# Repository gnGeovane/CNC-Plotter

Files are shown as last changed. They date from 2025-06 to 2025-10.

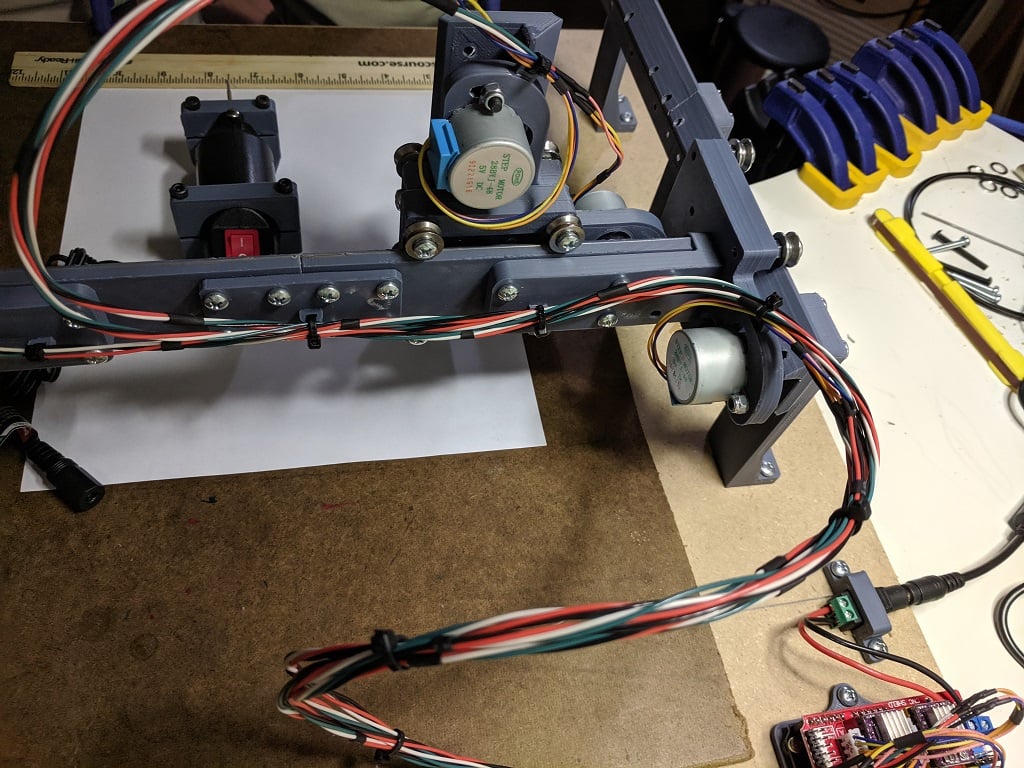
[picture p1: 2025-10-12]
Modelos 3D/Fully 3D Printed Small CNC Router_Plotter - 3842401 - part 1 of 2/images/Back_Overall-1.jpg

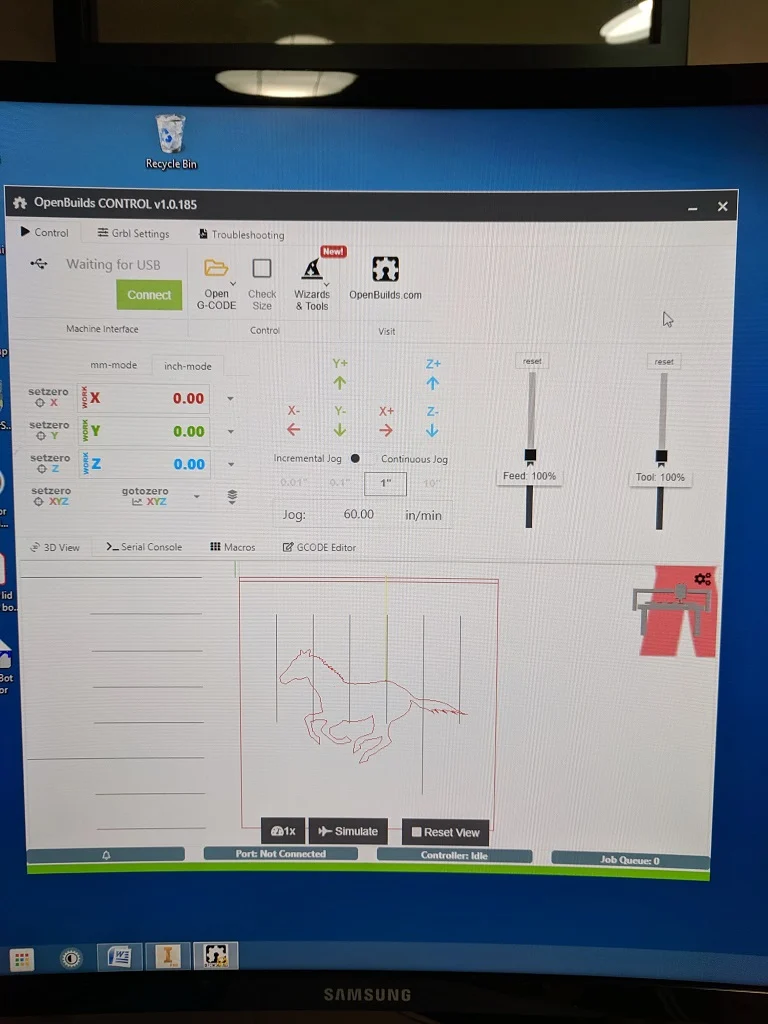
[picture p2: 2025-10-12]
Modelos 3D/Fully 3D Printed Small CNC Router_Plotter - 3842401 - part 1 of 2/images/OpenBuilds_Control_Screen_Shot-1.jpg

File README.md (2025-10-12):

# CNC-Plotter

Aqui você encontrará os arquivos necessários para fazer uma CNC Plotter e controlá-la.

# Código:

Todos os códigos e a biblioteca para motores de passo foram feitos do zero, linha-a-linha, especificamente para este projeto.
  
As versões mais recentes do código para o arduino incluem suporte para:

- Drivers de motores de passo L293D, ULN2803 e ULN2003;
- Sensores de fim de curso;
- Botão stop;
- Controle de motores de passo com ShiftRegister 74595 usando FullSteps e HalfSteps;
- Motores de passo bipolares ou unipolares.

# G-CODE Sender

Captura de tela 2025-06-23 110918

Para a comunicação do computador com o arduino para o envio do G-CODE do desenho, foi feito um G-CODE Sender do zero, programado no processing 4.
Este arquivo, quando executado no compilador processing, cria uma interface gráfica simples mostrando os comandos de controle da CNC, como:

- Movimentar algum eixo;
- Subir e descer a caneta;
- Ir para a posição Home;
- Buscar um arquivo G-CODE no Windows Explorer e iniciar o envio serial.

# APP para android

Também foi criado um app em Kotlin no Android Studio que funciona de forma similar ao programa G-CODE Sender do item anterior. Porém, o diferencial do app para celular é a possibilidade de controlar a máquina à distância via Bluetooth.

Adobe Express - file
<br> Demonstração do app aqui: https://youtu.be/cIXA6mVwmhk

# Criação de G-CODE

Para criar o arquivo de coordenadas (G-CODE) de uma imagem para desenhá-la, é necessário utilizar o software InksCape (gratuito) ou Autodesk ArtCAM (Pago). Caso queira plotar um circuito em uma PCB, poderá converter arquivos Gerber(.gbr) e Excellon(.drl) em G-CODE utilizando o software de código aberto FlatCAM.
  
# Veja os resultados atuais do projeto:

 CNC

IMG_20251009_102834619_HDR

<br> Desenhos

Desenhos

Captura de tela 2025-06-23 113415

# Assista a CNC em ação no YouTube!

[Desenhando ícone do app (controle por Bluetooth com app)](https://youtu.be/TSL-Wnw5sp4)

<a href="https://youtu.be/TSL-Wnw5sp4">
  Desenhando ícone do app
</a>

<br> [Desenhando um avião (controle via porta serial)](https://www.youtube.com/watch?v=H5-JilG_zv4)

<a href="https://www.youtube.com/watch?v=H5-JilG_zv4">
  Desenhando um avião
</a>

<br> [short - Desenhando um touro (Controle via porta serial)](https://www.youtube.com/shorts/jxCdN6tVYik)

<a href="https://www.youtube.com/shorts/jxCdN6tVYik">
  Desenhando um touro
</a>

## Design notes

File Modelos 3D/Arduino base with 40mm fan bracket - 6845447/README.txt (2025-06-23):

Arduino base with 40mm fan bracket by thrly on Thingiverse: https://www.thingiverse.com/thing:6845447

Summary:
An alternative for Andrew Sleigh's brilliant pen plotter (mk.3) arduino/cnc shield box. This is a much quicker print, and leaves the boards open with space for heatsinks and a side bracket for mounting a small 40mm fan. (The fan just runs straight off the 5V/GND pins on the CNC shield).Fan bracket takes M3 bolts/nuts.Details: https://github.com/thrly/plotter

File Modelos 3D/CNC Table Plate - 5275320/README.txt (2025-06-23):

CNC Table Plate by gcarlyle22 on Thingiverse: https://www.thingiverse.com/thing:5275320

Summary:
I made a CNC plotter for PC boards and couldn't find anything to hold them to the bed. So here is my working table.

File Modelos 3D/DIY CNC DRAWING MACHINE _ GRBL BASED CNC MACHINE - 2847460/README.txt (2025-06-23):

DIY CNC DRAWING MACHINE | GRBL BASED CNC MACHINE by electricdiylab on Thingiverse: https://www.thingiverse.com/thing:2847460

Summary:
JLCPCB (10 boards for $ 2) &amp; Free shipping: https://jlcpcb.comhttps://youtu.be/qOcFgiuLx3kMaterial I UsedArduino UNO :- https://www.amazon.in/gp/product/B015C7SC5U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 CNC shield :- https://www.amazon.in/gp/product/B015C7SC5U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 Stepper driver (2qty) :- https://www.amazon.in/gp/product/B015C7SC5U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 pro servo motor :- https://www.amazon.in/gp/product/B015C7SC5U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 SUPPLY  : - https://goo.gl/FKbxF66MM Smooth rod :- https://www.amazon.in/gp/product/B015C7SC5U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 motor :-    https://goo.gl/w9hHG3Timing belt :- https://www.amazon.in/gp/product/B015C7SC5U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 :- https://www.amazon.in/gp/product/B015C7SC5U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 pulley :- https://www.amazon.in/gp/product/B015C7SC5U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 x 20 aluminium frameLink to download : -MI Inkscape Extension.zip : - https://www.mediafire.com/file/9x1m60w1x6tdhaw/MI%20Inkscape%20Extension.zipMIGRBL.zip :-https://www.mediafire.com/file/wxsy99vzdu6dlvg/MIGRBL.zipCNC - Shield v3 01 WIRING.pnghttps://www.mediafire.com/file/53c8ywmb4aw69k9/CNC%20-%20Shield%20v3%2001%20WIRING.pngGRBL Controller :-https://github.com/zapmaker/GrblHoming/releases/download/v3.6.1/GrblController361Setup.exevisit for morehttp://electricdiylab.com/

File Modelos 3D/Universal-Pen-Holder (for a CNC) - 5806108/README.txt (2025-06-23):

Universal-Pen-Holder (for a CNC) by ZenziWerken on Thingiverse: https://www.thingiverse.com/thing:5806108

Summary:
Every now and then I thought about how the CNC machine could be used as a plotter. Of course, the Z-axis, which is driven by a stepper motor, is only conditionally suitable, but at least the positioning accuracy should be clearly superior to the belt-driven plotters. So all that's really missing is a spring-loaded mounting for the pen. This holder is so universal that you can use any pen you like. In a first attempt, I designed a version that accepts a classic Rapidograph (ink pen with capillary nib). But first of all this design was not usable for other pens, furthermore the linear movement was not precise enough.To solve the problem I got a mini linear rail. This was mounted on parts made of PMMA. I have already used this material in other projects. When heated with a heat gun, it can be bent into shape quite well. The result was already good, but the PMMA was not stable enough. Besides, it is difficult to cut threads in PMMA.This is how the final version was made. 3 mm thick aluminum is used. It has slots at the appropriate places, which make cold forming relatively easy. The bending radius is therefore very small. The quite large material thickness allows a reasonable use of taps, so that some screw connections can do without nuts.Please be aware that the stl-file is for viewing purpose only. Don't print this design on a fdm-printer!Visit https://www.zenziwerken.de/en/ for more interesting designs.

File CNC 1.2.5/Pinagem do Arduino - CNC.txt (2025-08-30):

Pinos do Arduino:

----------------------------------------------------------------------------------
11(RX), 12(TX): Módulo Bluetooth (VISÃO DO ARDUINO)
----------------------------------------------------------------------------------
A4, A5:  I2C
----------------------------------------------------------------------------------

----------------------------------------------------------------------------------
0, 1: comunicação serial
----------------------------------------------------------------------------------
2: Sem uso
----------------------------------------------------------------------------------
3: PLANNER
----------------------------------------------------------------------------------
A0:    DUAS FUNÇÕES: PAUSE(click) e AJUSTAR POSIÇÃO(PRESSIONE POR 0,5s)
----------------------------------------------------------------------------------
A1:    SENSOR DE FIM DE CURSO (X0)
----------------------------------------------------------------------------------
A2:    SENSOR DE FIM DE CURSO (Y1)
----------------------------------------------------------------------------------

----------------------------------------------------------------------------------
7, 5, 6, 4: CONTROLE DO EIXO Z
----------------------------------------------------------------------------------
8, 9, 10: SHIFT RETGISTER EIXO X/Y
----------------------------------------------------------------------------------

livres: A3, 13

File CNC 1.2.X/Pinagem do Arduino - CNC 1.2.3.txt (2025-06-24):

Pinos do Arduino:

----------------------------------------------------------------------------------
3(RX), 4(TX): Módulo Bluetooth
----------------------------------------------------------------------------------
A4, A5:  I2C
----------------------------------------------------------------------------------

----------------------------------------------------------------------------------
0, 1: comunicação serial
----------------------------------------------------------------------------------
2: Sem uso
----------------------------------------------------------------------------------
9:    SENSOR DE FIM DE CURSO (X0)
----------------------------------------------------------------------------------
10:    SENSOR DE FIM DE CURSO (Y1)
----------------------------------------------------------------------------------
A0:    AJUSTAR POSIÇÃO (BOT)
----------------------------------------------------------------------------------
A1:    PLANNER
----------------------------------------------------------------------------------

----------------------------------------------------------------------------------
5, 6, 7, 8: IN Z
----------------------------------------------------------------------------------
11, 12, 13:      SHIFT RETGISTER X/Y
----------------------------------------------------------------------------------

livres: A2, A3

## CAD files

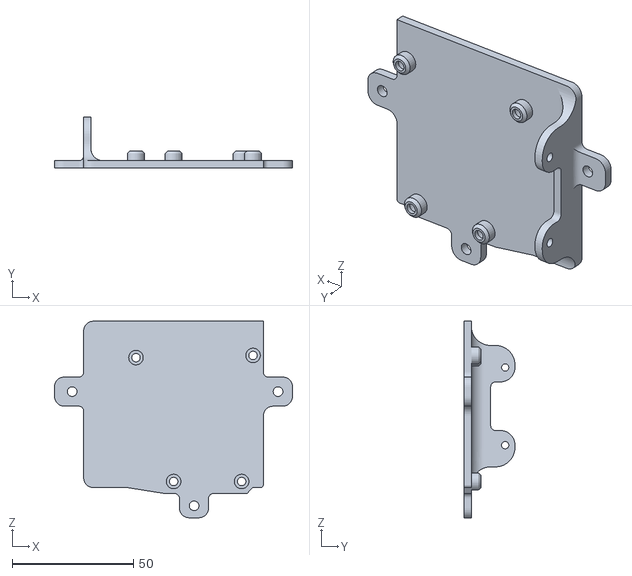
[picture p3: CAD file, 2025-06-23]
Modelos 3D/Arduino base with 40mm fan bracket - 6845447/files/arduino-bracket-with-fan.stl
98.0 x 21.0 x 81.0

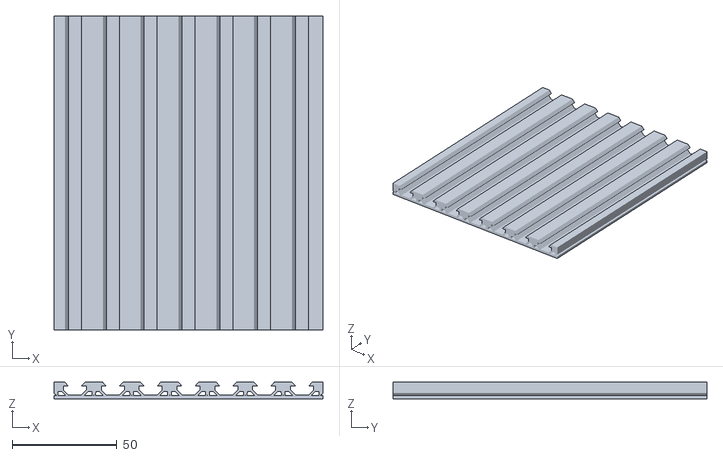
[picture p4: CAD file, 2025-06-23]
Modelos 3D/CNC Table Plate - 5275320/files/Table_V_Slot_Double.stl
128.6 x 150.0 x 7.90

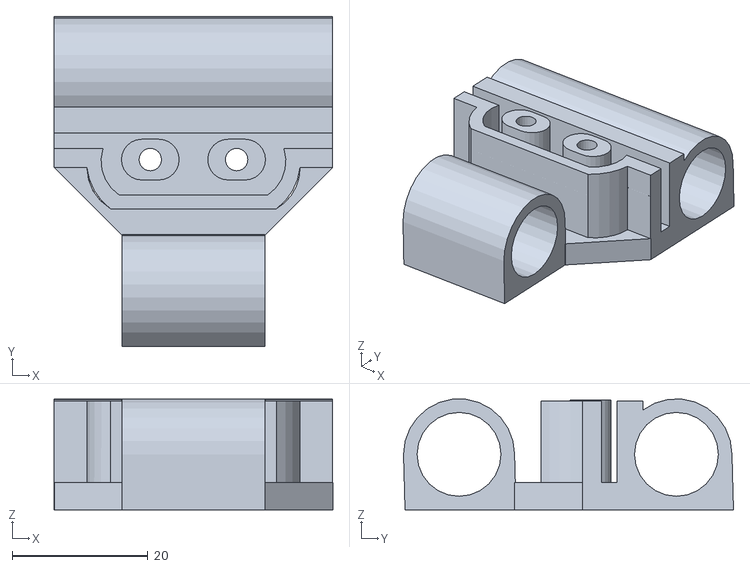
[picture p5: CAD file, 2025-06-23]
Modelos 3D/DIY CNC DRAWING MACHINE _ GRBL BASED CNC MACHINE - 2847460/files/c.stl
41.0 x 48.6 x 16.3

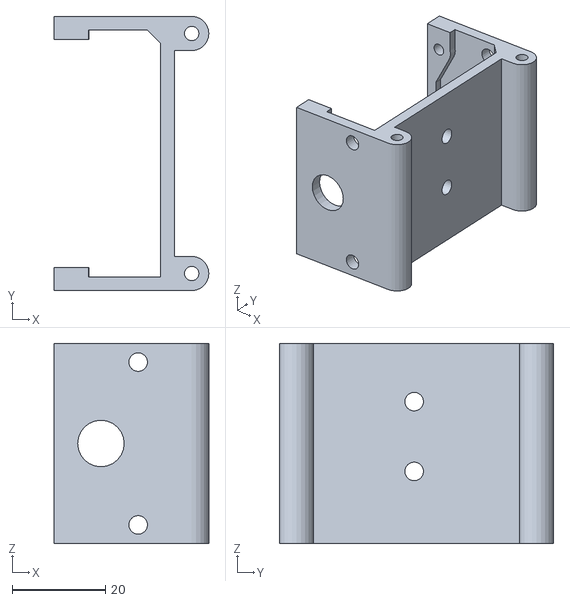
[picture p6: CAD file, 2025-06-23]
Modelos 3D/English and Spanish Mini CNC Plotter With CNC SHIELD, Arduino and Step motor 28BYJ-28 - 2985627/files/X_AXIS_PLATFORMMOD.stl
33.3 x 59.0 x 43.0

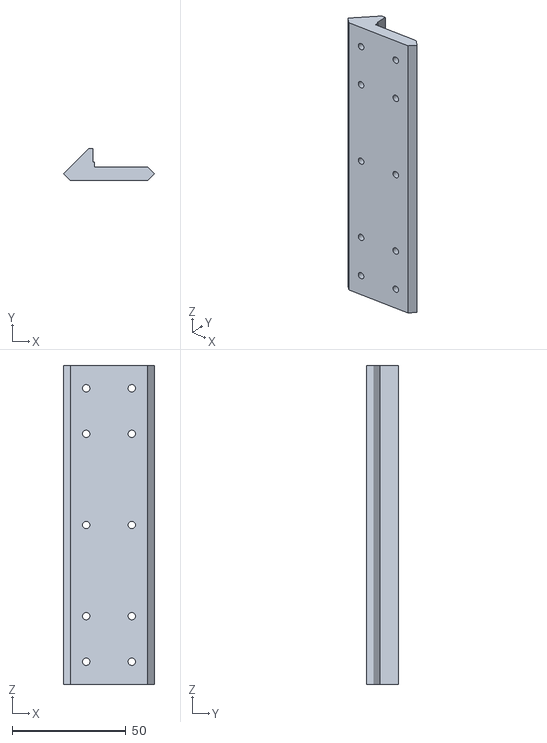
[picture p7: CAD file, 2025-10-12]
Modelos 3D/Fully 3D Printed Small CNC Router_Plotter - 3842401 - part 1 of 2/files/Linear_Rail_140mm.stl
40.0 x 14.0 x 140.0

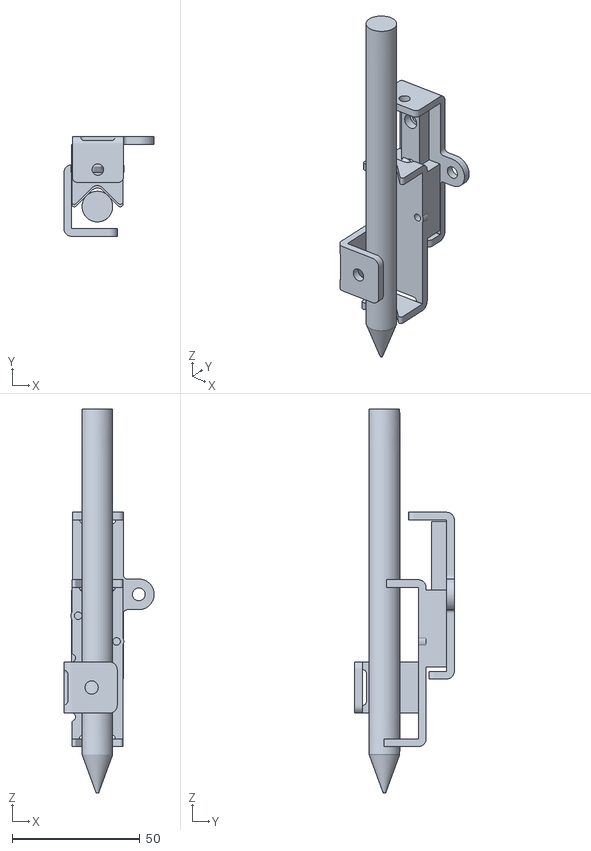
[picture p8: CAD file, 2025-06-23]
Modelos 3D/Universal-Pen-Holder (for a CNC) - 5806108/files/Universal-Pen-Holder.stl
35.3 x 39.0 x 150.0

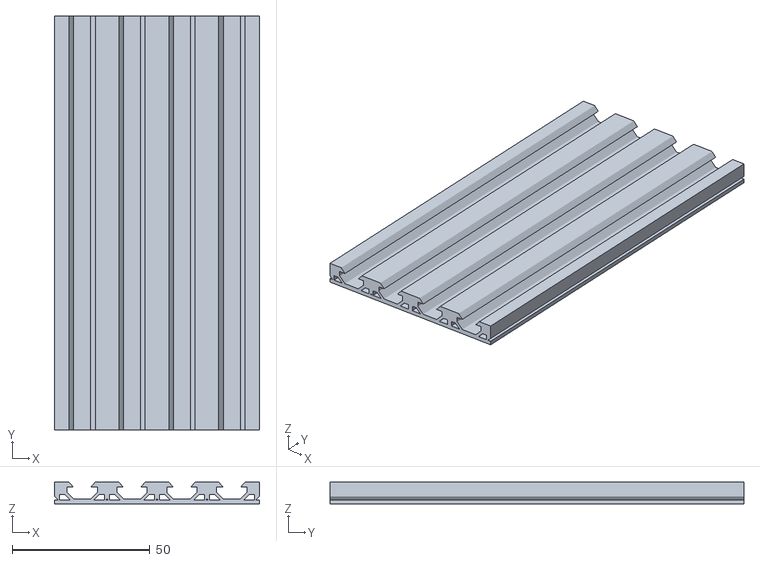
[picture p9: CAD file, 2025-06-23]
Modelos 3D/CNC Table Plate - 5275320/files/Table_V_Slot.stl
74.3 x 150.0 x 7.90

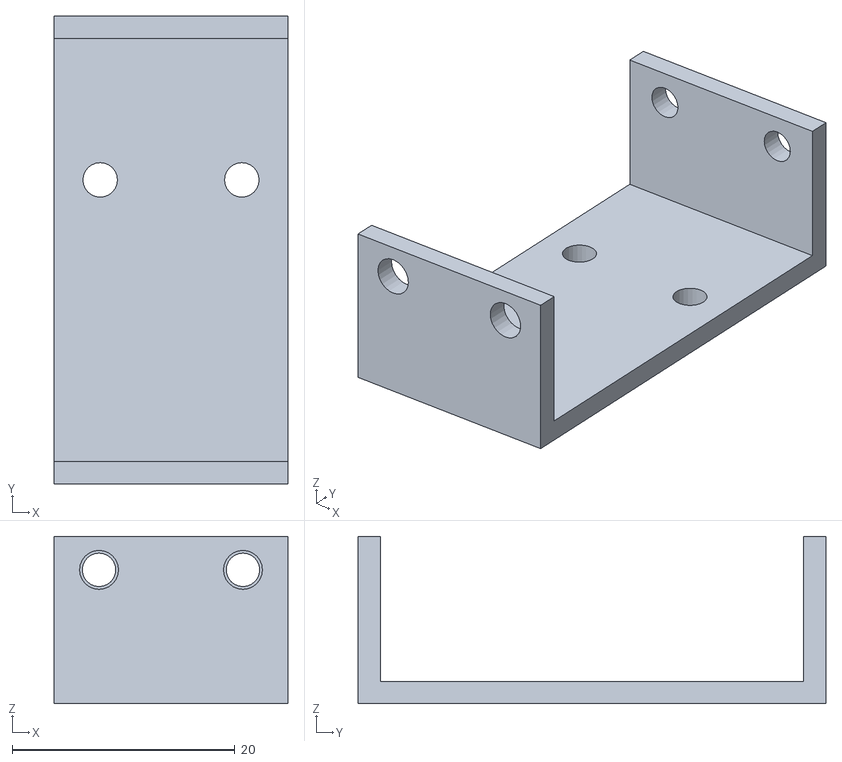
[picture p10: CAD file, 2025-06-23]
Modelos 3D/DIY CNC DRAWING MACHINE _ GRBL BASED CNC MACHINE - 2847460/files/d.stl
21.0 x 42.0 x 15.0

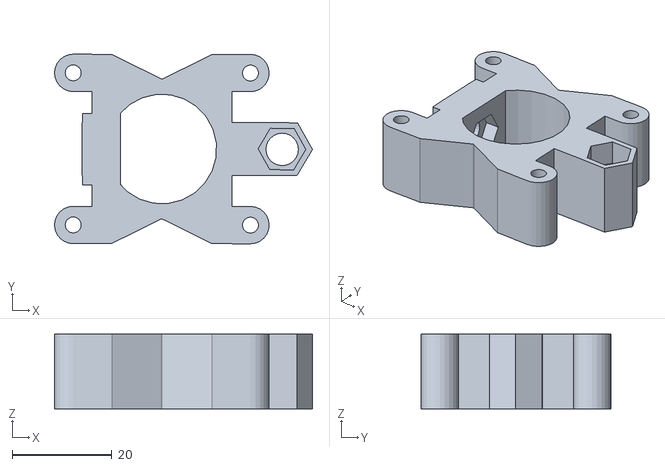
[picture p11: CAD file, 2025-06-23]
Modelos 3D/English and Spanish Mini CNC Plotter With CNC SHIELD, Arduino and Step motor 28BYJ-28 - 2985627/files/Spindle_Holder.stl
51.7 x 38.0 x 15.0

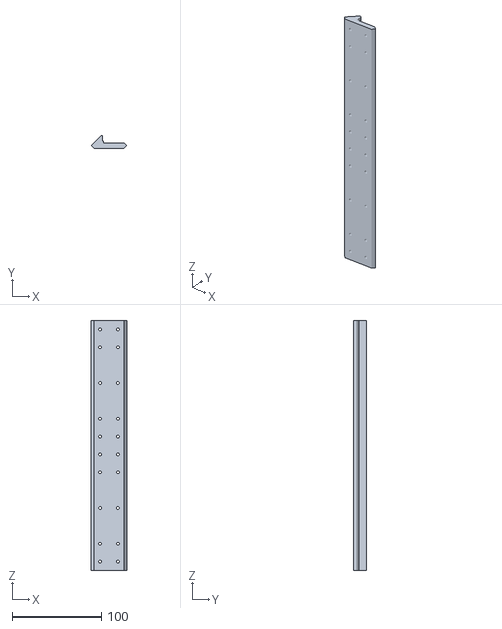
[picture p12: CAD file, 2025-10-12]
Modelos 3D/Fully 3D Printed Small CNC Router_Plotter - 3842401 - part 1 of 2/files/Linear_Rail_280mm.stl
40.0 x 14.0 x 280.0

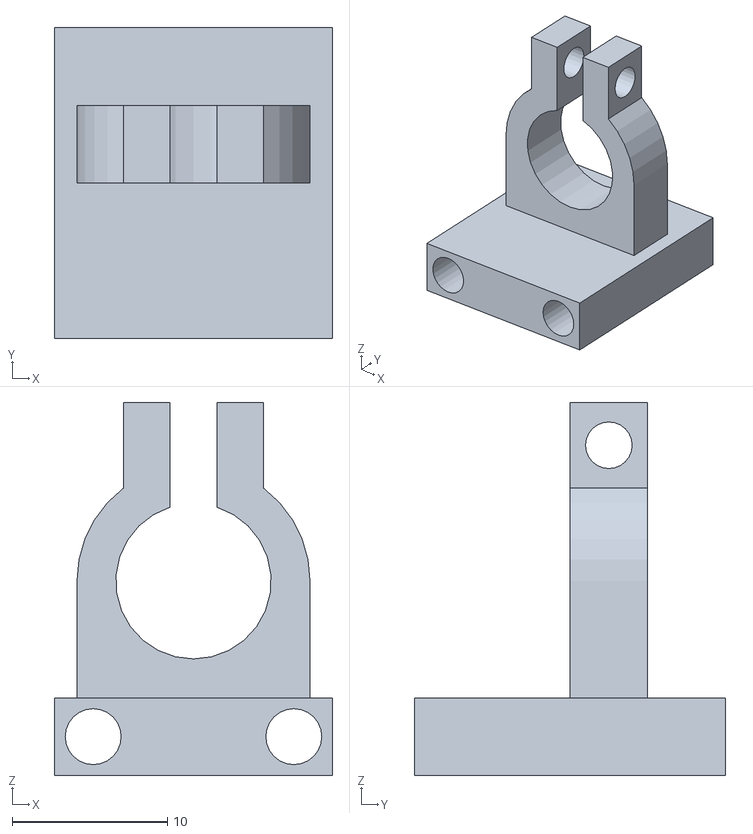
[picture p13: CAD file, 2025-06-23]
Modelos 3D/DIY CNC DRAWING MACHINE _ GRBL BASED CNC MACHINE - 2847460/files/E.stl
17.9 x 20.0 x 24.0

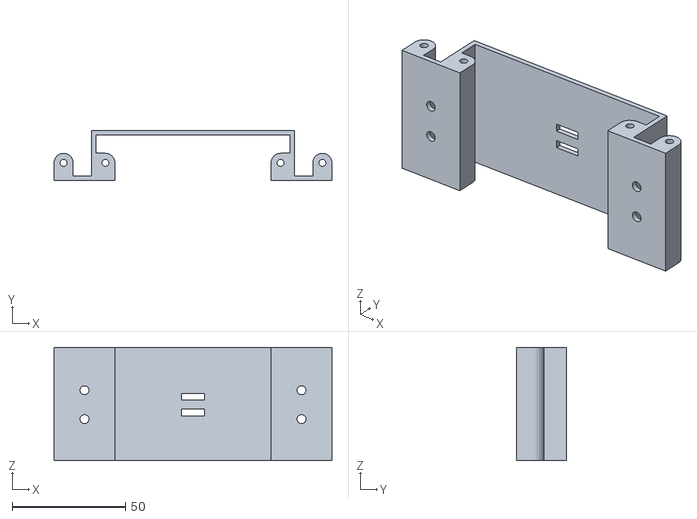
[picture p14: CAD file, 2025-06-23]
Modelos 3D/English and Spanish Mini CNC Plotter With CNC SHIELD, Arduino and Step motor 28BYJ-28 - 2985627/files/Y_Slider_Rail_Unidos.stl
123.0 x 22.0 x 50.0

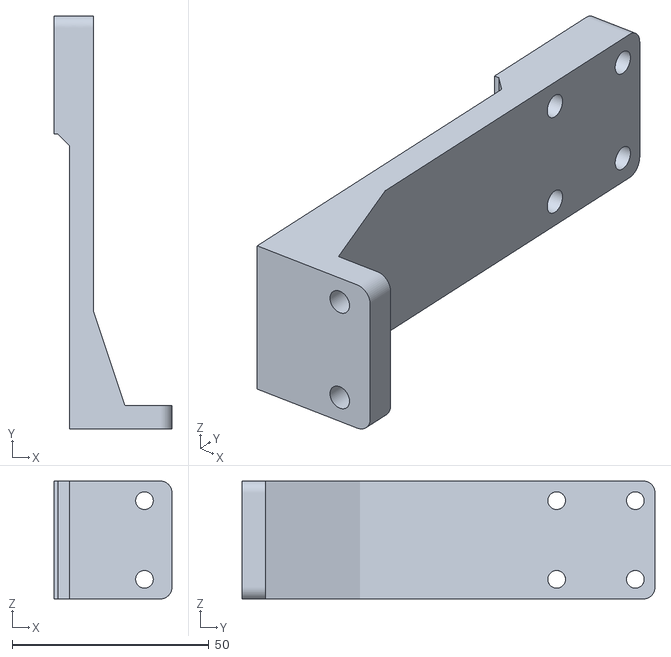
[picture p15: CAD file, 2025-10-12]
Modelos 3D/Fully 3D Printed Small CNC Router_Plotter - 3842401 - part 1 of 2/files/Leg.stl
30.0 x 105.0 x 30.0

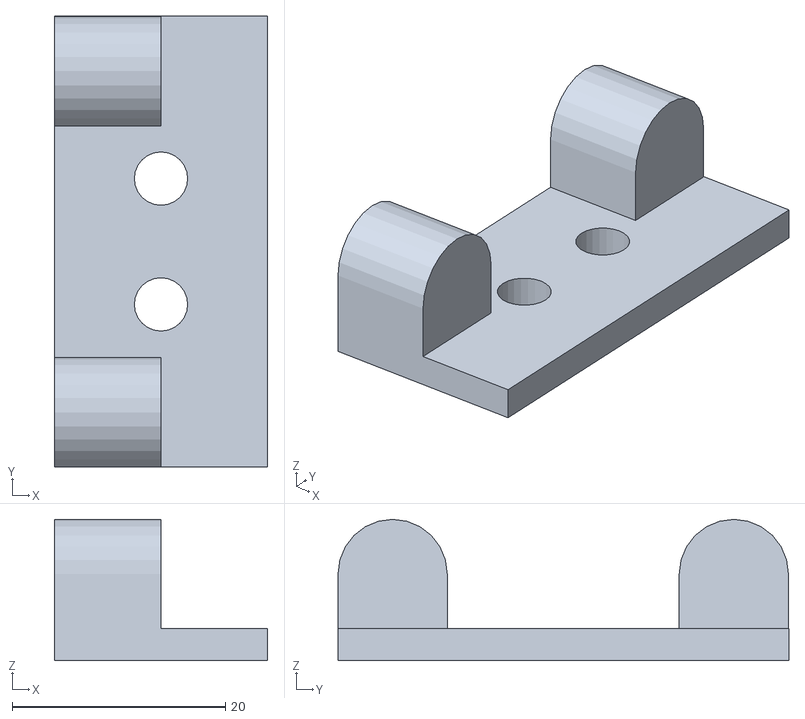
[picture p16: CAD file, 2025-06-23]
Modelos 3D/DIY CNC DRAWING MACHINE _ GRBL BASED CNC MACHINE - 2847460/files/b.stl
20.0 x 42.3 x 13.2

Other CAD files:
Modelos 3D/English and Spanish Mini CNC Plotter With CNC SHIELD, Arduino and Step motor 28BYJ-28 - 2985627/files/Y_Motor_Mount.stl
Modelos 3D/Fully 3D Printed Small CNC Router_Plotter - 3842401 - part 1 of 2/files/Zip_Tie_Holder.stl
Modelos 3D/DIY CNC DRAWING MACHINE _ GRBL BASED CNC MACHINE - 2847460/files/a.stl
Modelos 3D/English and Spanish Mini CNC Plotter With CNC SHIELD, Arduino and Step motor 28BYJ-28 - 2985627/files/YAxis_Rail_Holder_mod.stl
Modelos 3D/English and Spanish Mini CNC Plotter With CNC SHIELD, Arduino and Step motor 28BYJ-28 - 2985627/files/Soporte_para_lapiz.stl
Modelos 3D/English and Spanish Mini CNC Plotter With CNC SHIELD, Arduino and Step motor 28BYJ-28 - 2985627/files/Z_AXIS_MOTOR_COUPLINGmod.stl
Modelos 3D/English and Spanish Mini CNC Plotter With CNC SHIELD, Arduino and Step motor 28BYJ-28 - 2985627/files/x_Motor_Mount.stl
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

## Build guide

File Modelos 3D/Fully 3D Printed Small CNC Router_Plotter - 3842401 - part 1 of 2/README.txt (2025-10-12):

Fully 3D Printed Small CNC Router/Plotter by cbc on Thingiverse: https://www.thingiverse.com/thing:3842401

Summary:
This Thing began as an effort to build a small, cheap CNC machine.  I mainly wanted to gain some experience with the electronics and control software without spending several hundred dollars on components.  For control it uses clones of an Arduino Uno and CNC V3 shield.  Steppers are the ultra cheap 28BYJ-48's with the bipolar hack.  The drive system is GT2 pulleys with belts glued to the linear rails used as a rack and pinion gear drive to reduce moving parts.  For a spindle I would try the tiny HF Drillmaster Rotary Tool (see edit below).  I did not want to buy rods or extrusions for the frame so all the other parts including linear rails would be 3D printed.   Plus all the parts had to fit on the 6"x 6" print bed of the Lulzbot Mini.  This is what I ended up with.  It is fairly small but still has 7"x 7"x 1.5 (177 x 177 x 40 mm) of travel with about 18" x 20" overall size.  It was fairly cheap (by CNC standards anyway).  It cost about $90.00 in purchased parts, plus whatever it cost me to print the parts.   As an exercise in learning the electronics it was excellent.  I learned plenty.  I will try to share what I learned.  It turns out in function it is more of a demo or Toy CNC.  Nod here to Thorgal's ToyREP 3D Printer (see build notes).   It is not really rigid enough to be called a real CNC machine but repeatability is surprisingly good.  It also moves well.  I have done plots at 60 in/min.  It gets glitchy above that but maybe some settings could be tweaked.  To be honest I haven't even tried the rotary tool for milling yet.  I have been focusing on holding pens.  As a pen plotter it is working great!  My granddaughter is fascinated by it and loves watching it draw.  She wants to learn to use it and that makes the whole build a win for me!  If it ever actually mills something or someday holds a laser cutter that will be a bonus.   Video: https://youtu.be/o14qxU9eJ0QRepeatability video: https://youtu.be/fjbzklIJpxMParts:Online Parts:Here are links to the parts I purchased on Amazon.  Cost might be less if you don't mind long ship times.Uno and CNC shield clone Kit:  $18.99This kit comes with limit switches that I have not used yet but will try to incorporate in the future.Stepper Motors  $10.39Steppers come with driver boards that you don't need.  Use the drivers in the CNC kit.  Motors will need to be modified to bipolar. GT2 Timing Belt    $7.99Timing Belt Pulleys   $5.99V Groove Wheels   $8.71Power Supply   $10.99I used a similar one I had on hand)Locally Sourced Parts:Lowes had M4 Phillips head machine screws (12 for $1.98).  You could save money by purchasing those online.  I used the Phillips head because they were cheaper than socket head (socket head screws would look better).  I did use socket head screws where I thought they would be more functional.   Most of those came from Ace Hardware.1/2"x 24"x 24" MDF   $3.84  (cut to required size)Spindle Motor   $9.99  Harbor Freight (less if you find a 25% off coupon)  I am sorry to report the Collet on this tool is not strong enough to hold the end mill in place.  See additional comments below.Build Notes:Motors/Electronics:The motors and electronics were the most difficult part of the build.  Wait, wasn't that why I did the build in the first place?  Anyway....a few lessons learned. I couldn't run the motors directly from the Arduino.  Well I could, but not all together as a CNC machine, you need the CNC Shield and drivers.  The CNC Shield will only drive bipolar steppers and the 28BYJ's are unipolar.  There is a popular hack to convert them to bipolar.  The bipolar hack is pretty straight forward (plenty of info on that online).  The only tricky part is getting the motor wires in the correct order.  I reused the connector.  My wire order is blue-yellow-orange-pink.  You can reverse the connector on the shield to reverse motor direction (lip on top of connector may need to be clipped).  Reversing is required for the cloned Y-axis motor.  I removed the red wire from the connector and cut it on the motor end.  The motor wires need to be cut and extended.  I used some 4 conductor 22 gage wire from the big box.  If you buy cheap clones like I did for the Arduino and CNC shield be careful with pin alignment.  I wasted several hours troubleshooting when one section of shield pins had missed the sockets on the Arduino.   Looked fine from the outside, pins missed to the inside.   The pins had to be straightened on the stepper drivers boards as well.Driving the motors:  Most of the following information I got from Thorgal's ToyREP 3D Printer here on Thingiverse.   I don't think I would ever have gotten my steppers working properly if I had not finally turned up his info on micro-stepping and voltage settings for the 28BYJ-48.  Thank you Thorgal!I did a lot of searches for 28BYJ-48 &amp; CNC.  Some of the info out there was good, some not so good.  Most of the mistakes were probably mine.  Bipolar Hack - good info.  How to adjust current on stepper driver - good info (but what is the correct setting for a 28BYJ?).  Don't need to micro-step a 28BYJ.  Bad info.  Theory says the 5.625 degree step angle divided by the 1:64 gear reduction give a full step as .088 degrees or 4096 steps per rev.  Those are pretty small full steps.  Probably works for straight Arduino control.  My motors didn't care.  Motors chattered, missed steps, ran slow and hot.  Set micro-stepping to 16 (jumper on shield).  Set voltage on driver board pots to .08 volts.  Motors run smooth, fast and cool.  Thanks again Thorgal!Control Software:I am using GRBL v1.1h (grbl_v1.1h.20190825.hex) loaded with Xloader to the Arduino.   There are plenty of tutorials on using Xloader.  The link to the original Xloader seems to be broken so I will upload a copy of the zip file.   Make sure the baud rate is set to 115200 in the Arduino serial monitor.  If it is set to 9600 you see 2 backward question marks when it tries to connect.  You should see "Grbl 1.1h ['$' for help]".  I am using the OpenBuilds Controller software on the computer to send G code and control the CNC.  This seems to be very nice software with lots of features and it looks good.  This only supports the 115200 baud rate and won't work with earlier versions of Grbl at 9600.  Grbl settings: Check the Axis directions and invert (or reverse the motor plugs) as required, steps/mm X, Y &amp; Z = 1024, acceleration X &amp;Y = 30, Z = 20.  Write down or copy your settings.  If you need to reload (or on some resets) Grbl you will lose your settings.For CAM I use Inventor (or Fusion 360) HSM with the Grbl milling post processor.  Set Output M6 and Output Tool Number to NO in the post processor dialog box in HSM.3D printed Parts:In addition to uploading the STL files I will be uploading STP and native Inventor files to facilitate modifications.  I will also include a 280 liner rail that can be printed in one piece on a larger (12"x 12") print bed.  I will also upload PDF files with a complete bill of materials and drawings with assembly instructions.Orientation on the build plate is straight forward.  I have posted a PDF with build orientation.  No supports were used for any of the parts.   I did set perimeter walls to 4.  This puts a little more material around the holes for tapping threads.  I have a .5mm nozzle.  I used 4 top and bottom layers with .25mm layer height.  I used ABS for all the parts.  Stiffer material like PLA or Nylon X might be better, but I tend to print everything in ABS.I was planning on switching out the pen holder and the spindle holder on the Z rail but now I am thinking it will be easier and quicker to print a Z rail for each holder and swap the rail and all.I am going to post the pen holder and the spindle holder as separate Things to try and keep this one organized.Link to Pen Holder here.Link to Spindle Holder here.Link to Dremel 2050 Stylo Spindle Holder here.Misc:To glue the GT-2 Belt to the Linear Rails I used Dap Rapidfuse.  I found it at the big boxes and it seems to do an excellent job gluing different materials together.  Use the small step on linear rail to help line the belt up.  Roll some of the belt back, apply glue to the rail and roll the belt back down.   When gluing the belt to the Y-axis rails try to start the first tooth in the same place.  This will help keep the X-axis square.  Remember the Y-axis rails are opposite hand.Use the Zip Tie Mounts and Zip Tie Holder(s) for cable management.  They are not shown on the drawings.  To glue Zip Tie Mounts to the drive carriages or X-axis rail use Plastruct Bondene.   The Zip Tie Holder is designed for a #4 flat head screw but I just glued it to the MDF with Rapidfuse.I am using a piece of 1/8" masonite clamped on top of the MDF as a replaceable spoil board.  The masonite is smoother than the MDF and pens write better on it.  They would probably write even better on acrylic.This is a work in progress and I will try post and new info and improvements as I go.  Any comments and suggestions for improvements would be welcome.Edit 9-3-19:  Added link to pen holdersAdded Link to Spindle Holder.Added Repeatability videoEdit 9-6-19:  The spindle Motor from Harbor Freight has a problem. The power is ok.  The problem is the collet on this tool is not strong enough to hold the end mill in place.  I was test milling on 1/8" acrylic.  I was able to mill the acrylic with shallow depth of cuts and was pleasantly surprised at how well it was cutting.  The problem was with holding the end mill in the collet.  I was using a .073" dia. (.125" shank) single flute end mill.  As I was running additional tests suddenly the mill would bury itself in the material.  The end mill was pulling itself out of the collet.  I tried to tighten the the knurled collet with pliers but it still pulled out.  Then I managed to damage the locking pin that keeps the shaft from turning so it no longer locks.  Time for a redesign using a tool with a better collet.  My searches turned up cheap tools but many comments on cheap collets.  Now I am looking at the Dremel Stylo 2050-15. It's 50 bucks.  That's more than half of what I had in the whole build.  Would be nice to be able to cut acrylic though.  If you only cut soft material like machinable wax the HF tool might work. Edit 9-12-2019:  Changed License type to Creative Commons - AttributionEdit 9-27-2019:  Added link to Dremel 2050 Stylo Spindle Holder

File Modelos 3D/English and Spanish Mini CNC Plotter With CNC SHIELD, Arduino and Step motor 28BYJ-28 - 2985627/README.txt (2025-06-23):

English and Spanish Mini CNC Plotter With CNC SHIELD, Arduino and Step motor 28BYJ-28 by lolivet on Thingiverse: https://www.thingiverse.com/thing:2985627

Summary:
EnglishMINI CNC Hi-TechWelcome to the Hi-Tech Electronics and Robotics tutorial to assemble our own small CNC machine for plotting ormill PCB boardsFirst we must have all the printed pieces which must have the following order:1 pcs X AXIS PLATAFORMMOD1 pcs Splindle Holder1 pcs Y Slider Rail Unidos4 pcs Yaxis Rail Holder Mod1 pcs Y Motor Mount1 pcs X Motor Mount1 pcs Soporte para Lapiz1 pcs Z AXIS MOTOR CouplingmodNOTE: All parts must be printed at 50% infill with a resolution of0.25mm (Layer Hight), 2 perimeters, 3 Top Solid Layers and 3 Bottom Solid Layer.If you want us to print it, it would be for a price of: Q410.00List of electronic and mechanical components of the CNC1 pcs CNC Shield with Arduino Uno R3 and 3 Original A4988 Drivers (Q350.00)3 pcs Stepper motors 28byj-48 hacked (Q45.00 C / U)1 pcs 9V Power Supply (Printer Source Q85.00)1 pcs 2 meters of toothed belt GT2 with 2 toothed pulleys (Q100.00)2 pcs 608z circular bearings without printing (Q30.00 C / U)28 Screws with nut M3 (Q2.50 C / U)10 Screws with nut M5 (Q2.75 C / U)NOTE: for the circular bearings, look for the pulley on the thing that you like the most.Help me grow my patreonhttps://www.patreon.com/lolivet/Assembly instructions watch the video.https://youtu.be/sw-cIN33urcEspañol MINI CNC Hi-TechBienvenido al tutorial de Electrónica y Robótica Hi-Techpara armar nuestra propia maquina CNC pequeña para plotear ohacer scarve en nuestras placas PCBPrimero debemos tener todas las piezas impresas las cuales deben tenerel siguiente Orden:1   X AXIS PLATAFORMMOD1   Splindle Holder1   Y Slider Rail Unidos4   Yaxis Rail Holder Mod1   Y Motor Mount1   X Motor Mount1   Soporte para Lapiz1   Z AXIS MOTOR CouplingmodNOTA: Todas las piezas se deben imprimir a 50% de infill con una resolucion de0.25mm (Layer Hight), 2 perimetros, 3 Top Solid Layers y 3 Bottom Solid Layer.Si quires que nosotros te lo imprimamos, seria por un precio de: Q410.00Listado de componentes electronicos y mecanicos de la CNC1   CNC Shield con Arduino Uno R3 y 3 Drivers A4988 Originales (Q350.00)3   Motor Stepp 28byj-48 hackeado (Q45.00 C/U)1   Fuente de Alimentacion 9V (Fuente de Impresora Q85.00)1   2 metros de correa dentada GT2 con 2 poleas dentadas (Q100.00)2   Rodamientos circulares 608z sin impresión (Q30.00 C/U)28  Tornillos con tuerca M3 (Q2.50 C/U)10  Tornillos con tuerca M5 (Q2.75 C/U)NOTA: para los rodamientos circulares buscar en thingivierse la polea que mas te guste.Ayudame a crecer se mi patreonhttps://www.patreon.com/lolivet/Instrucciones para ensamble ver el vídeo.https://youtu.be/sw-cIN33urc

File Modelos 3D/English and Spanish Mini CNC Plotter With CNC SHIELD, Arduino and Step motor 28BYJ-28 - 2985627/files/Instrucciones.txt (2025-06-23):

MINI CNC Hi-Tech
Bienvenido al tutorial de Electrónica y Robótica Hi-Tech
para armar nuestra propia maquina CNC pequeña para plotear o 
hacer scarve en nuestras placas PCB

Primero debemos tener todas las piezas impresas las cuales deben tener 
el siguiente Orden:

1	X AXIS PLATAFORMMOD
1	Splindle Holder
1	Y Slider Rail Unidos
4	Yaxis Rail Holder Mod
1	Y Motor Mount
1	X Motor Mount
1	Soporte para Lapiz
1	Z AXIS MOTOR Couplingmod

NOTA: Todas las piezas se deben imprimir a 50% de infill con una resolucion de 
0.25mm (Layer Hight), 2 perimetros, 3 Top Solid Layers y 3 Bottom Solid Layer.
Si quires que nosotros te lo imprimamos, seria por un precio de: Q410.00

Listado de componentes electronicos y mecanicos de la CNC

1	CNC Shield con Arduino Uno R3 y 3 Drivers A4988 (Q350.00)
3	Motor Stepp 28byj-48 hackeado (Q45.00 C/U)
1	Fuente de Alimentacion 9V (Fuente de Impresora Q85.00)
1	2 metros de correa dentada GT2 con 2 poleas dentadas (Q100.00)
2	Rodamientos circulares 608z sin impresion (Q30.00 C/U)
28	Tornillos con tuerca M3 (Q2.50 C/U)
10	Tornillos con tuerca M5 (Q2.75 C/U)

NOTA: para los rodamientos circulares buscar en thingivierse la polea que mas te guste.

Instrucciones para ensamble Ver el video.

Acá te dejo la descargas para que puedas utilizar tu mini cnc una vez armada

Librería GRBL que deberás cargar en el Arduino para que reconozca la CNC Shield y los motores:

http://www.mediafire.com/file/u5dwi73bba91fo0/GRBL%20para%20Arduino.rar

Programa para poder configurar y operar nuestra MINI CNC

http://www.mediafire.com/file/i7xlj4s27cp373v/GrblController361Setup.rar
http://www.mediafire.com/file/2b5i38sofgz7rwu/UniversalGcodeSender.zip
http://www.mediafire.com/file/ac3m6jhl83z3uah/ugsplatform.zip (este es el que mas recomiendo).

y por ultimo el programa utilizado para generar los archivos a dibujar
http://www.mediafire.com/file/1gl1vqsds2q9c3y/inkscape-0.92.3-x64.rar

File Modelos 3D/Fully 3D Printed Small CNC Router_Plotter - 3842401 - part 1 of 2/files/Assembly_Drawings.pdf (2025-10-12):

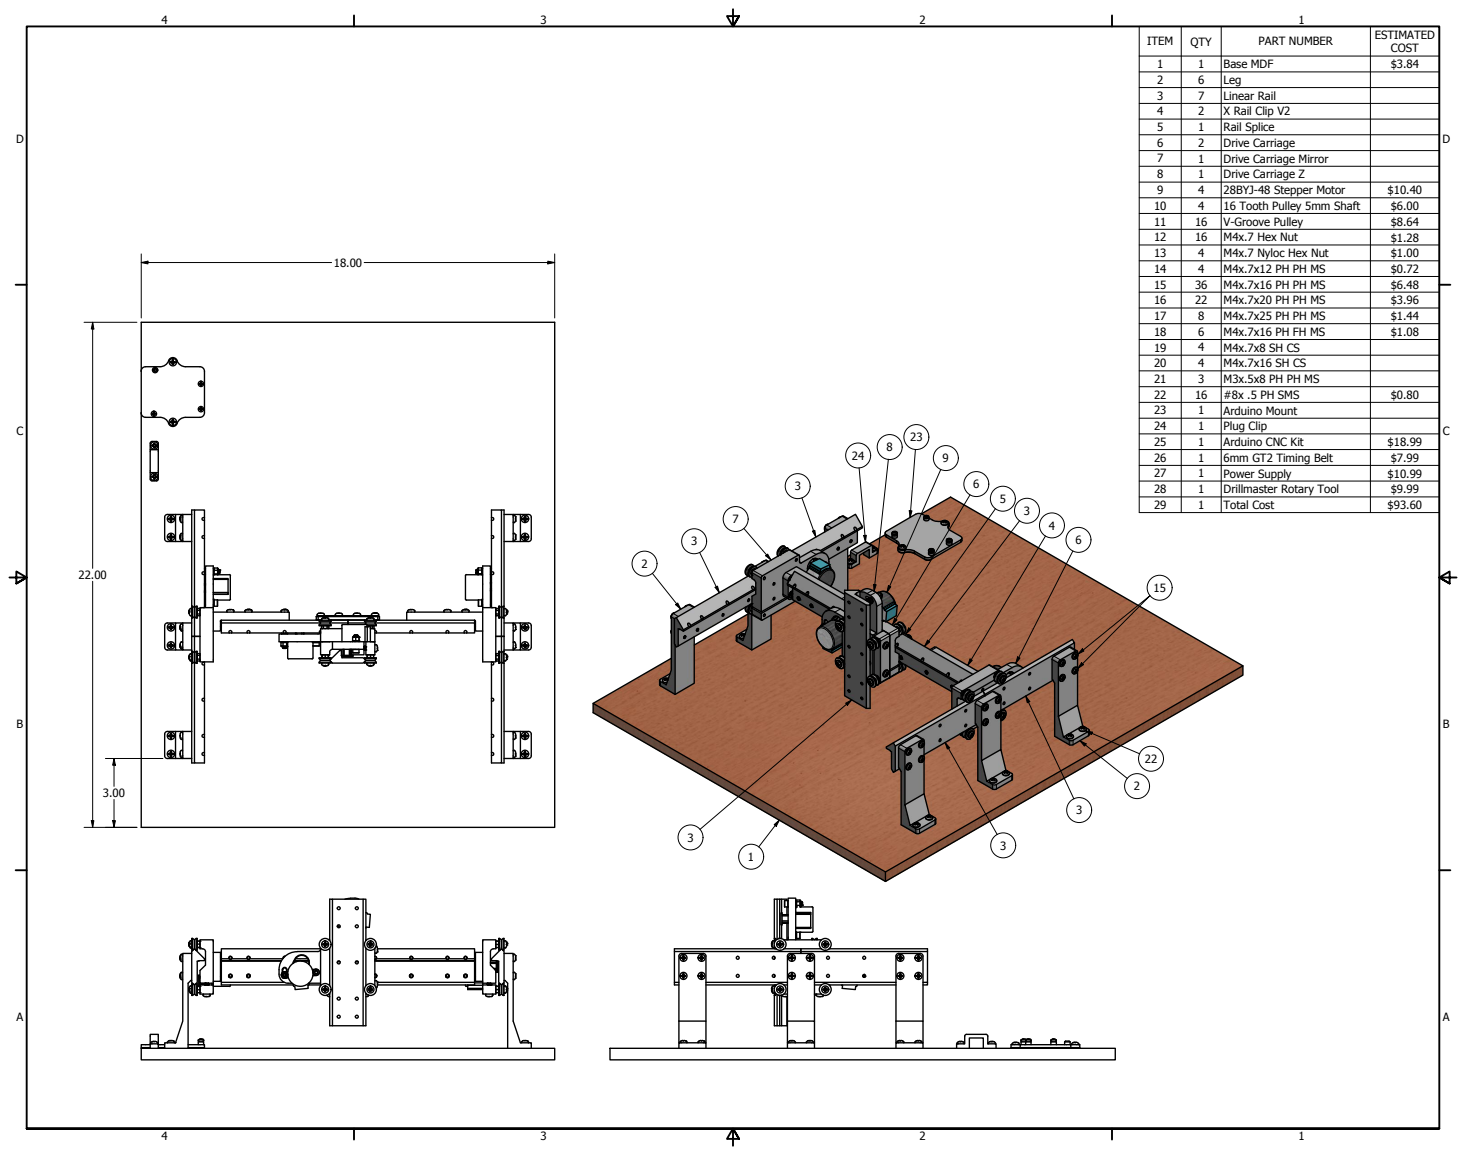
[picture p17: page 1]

B a s e M D F | $ .
L e g

3 | 7 2 | L X Rail Clip i n e a r R a il 4

5 | 1 | R a il S pli c e
6 | 2 | D r i v e C a r r i a g e
7 | 1 | D r i v e C a r r i a g e M i r r o r
8 | 1 | D r i v e C a r r i a g e Z
9 | 4 | 2 8 B YJ -4 8 S t e p p e r M o t o r | $ 1 0 . 4 0
1 0 | 4 | 1 6 T o o t h P ulle y 5 m m S h a ft | $ 6 . 0 0
1 1 | 1 6 | V -G r o o v e P ulle y | $ 8 . 6 4
1 2 | 1 6 | M 4 x . 7 H e x N u t | $ 1 . 2 8
1 3 | 4 | M 4 x . 7 N ylo c H e x N u t | $ 1 . 0 0
1 4 | 4 | M 4 x . 7 x 1 2 P H P H M S | $ 0 . 7 2
1 5 | 3 6 | M 4 x . 7 x 1 6 P H P H M S | $ 6 . 4 8
1 6 | 2 2 | M 4 x . 7 x 2 0 P H P H M S | $ 3 . 9 6
1 7 | 8 | M 4 x . 7 x 2 5 P H P H M S | $ 1 . 4 4
1 8 | 6 | M 4 x . 7 x 1 6 P H F H M S | $ 1 . 0 8
1 9 | 4 | M 4 x . 7 x 8 S H C S
2 0 | 4 | M 4 x . 7 x 1 6 S H C S
2 1 | 3 | M 3 x . 5 x 8 P H P H M S
2 2 | 1 6 | # 8 x . 5 P H S M S | $ 0 . 8 0
2 3 | 1 | A r d u i n o M o u n t
2 4 | 1 | Plu g Cli p
2 5 | 1 | A r d u i n o C N C K i t | $ 1 8 . 9 9
2 6 | 1 | 6 m m G T 2 T i m i n g B elt | $ 7 . 9 9
2 7 | 1 | P o w e r S u p ply | $ 1 0 . 9 9
2 8 | 1 | D r illm a s t e r R o t a r y T o ol | $ 9 . 9 9
2 9 | 1 | T o t al C o s t | $ 9 3 . 6 0

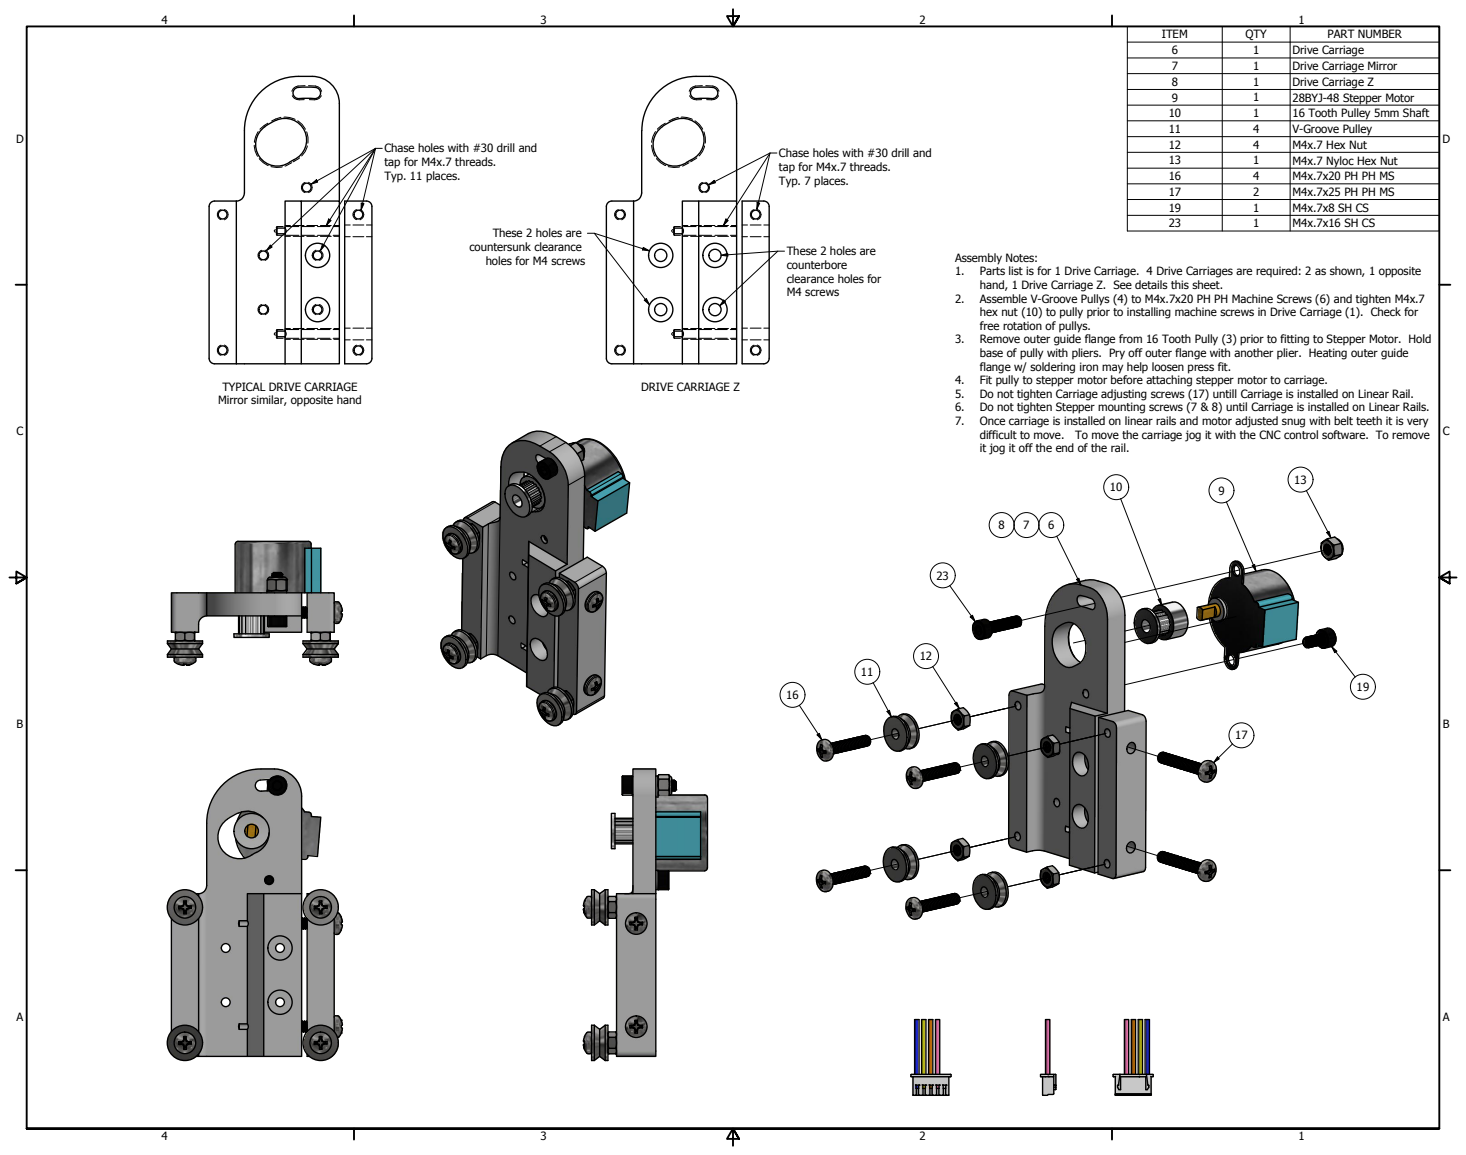
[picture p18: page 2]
DRIVE CARRIAGE Z

ITEM | QTY | PART NUMBER
6 | 1 | Drive Carriage
7 | 1 | Drive Carriage Mirror
8 | 1 | Drive Carriage Z
9 | 1 | 28BYJ-48 Stepper Motor
10 | 1 | 16 Tooth Pulley 5mm Shaft
11 | 4 | V-Groove Pulley
12 | 4 | M4x.7 Hex Nut
13 | 1 | M4x.7 Nyloc Hex Nut
16 | 4 | M4x.7x20 PH PH MS
17 | 2 | M4x.7x25 PH PH MS
19 | 1 | M4x.7x8 SH CS
23 | 1 | M4x.7x16 SH CS

Chase holes with #30 drill and
tap for M4x.7 threads.
Typ. 11 places.

Typ. 7 places.

These 2 holes are
countersunk clearance
holes for M4 screws

counterbore
clearance holes for
M4 screws

Assembly Notes:
1. Parts list is for 1 Drive Carriage. 4 Drive Carriages are required: 2 as shown, 1 opposite
hand, 1 Drive Carriage Z. See details this sheet.
2. Assemble V-Groove Pullys (4) to M4x.7x20 PH PH Machine Screws (6) and tighten M4x.7
hex nut (10) to pully prior to installing machine screws in Drive Carriage (1). Check for
free rotation of pullys.
3. Remove outer guide flange from 16 Tooth Pully (3) prior to fitting to Stepper Motor. Hold
base of pully with pliers. Pry off outer flange with another plier. Heating outer guide
flange w/ soldering iron may help loosen press fit.
4. Fit pully to stepper motor before attaching stepper motor to carriage.
5. Do not tighten Carriage adjusting screws (17) untill Carriage is installed on Linear Rail.
6. Do not tighten Stepper mounting screws (7 & 8) until Carriage is installed on Linear Rails.
7. Once carriage is installed on linear rails and motor adjusted snug with belt teeth it is very
difficult to move. To move the carriage jog it with the CNC control software. To remove
it jog it off the end of the rail.

TYPICAL DRIVE CARRIAGE
Mirror similar, opposite hand

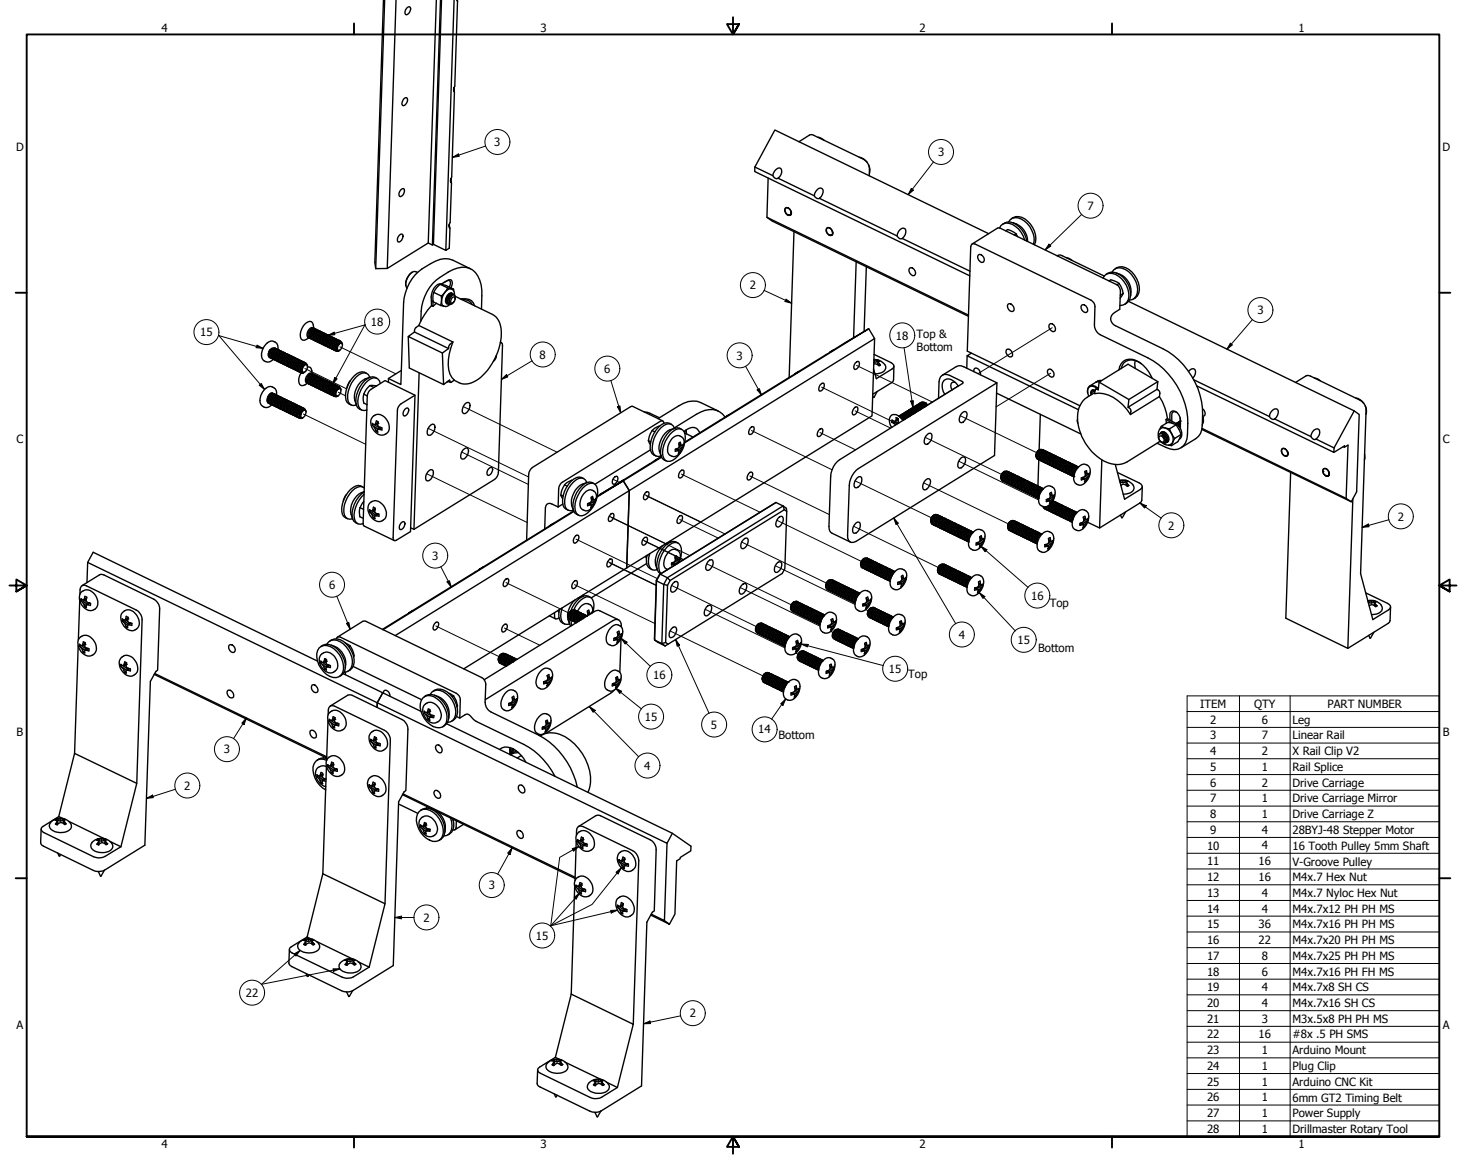
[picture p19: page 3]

I T E M | Q TY | P A RT N U M B E R
2 | 6 | L e g
3 | 7 2 | L X Rail Clip i n e a r R a il 4

5 | 1 | R a il S pli c e
6 | 2 | D r i v e C a r r i a g e
7 | 1 | D r i v e C a r r i a g e M i r r o r
8 | 1 | D r i v e C a r r i a g e Z
9 | 4 | 2 8 B YJ -4 8 S t e p p e r M o t o r
1 0 | 4 | 1 6 T o o t h P ulle y 5 m m S h a ft
1 1 | 1 6 | V -G r o o v e P ulle y
1 2 | 1 6 | M 4 x . 7 H e x N u t
1 3 | 4 | M 4 x . 7 N ylo c H e x N u t
1 4 | 4 | M 4 x . 7 x 1 2 P H P H M S
1 5 | 3 6 | M 4 x . 7 x 1 6 P H P H M S
1 6 | 2 2 | M 4 x . 7 x 2 0 P H P H M S
1 7 | 8 | M 4 x . 7 x 2 5 P H P H M S
1 8 | 6 | M 4 x . 7 x 1 6 P H F H M S
1 9 | 4 | M 4 x . 7 x 8 S H C S
2 0 | 4 | M 4 x . 7 x 1 6 S H C S
2 1 | 3 | M 3 x . 5 x 8 P H P H M S
2 2 | 1 6 | # 8 x . 5 P H S M S
2 3 | 1 | A r d u i n o M o u n t
2 4 | 1 | Plu g Cli p

A r d u i n o C N C K i t
m m G T T i m i n g B elt
P o w e r S u p ply
D r illm a s t e r R o t a r y T o

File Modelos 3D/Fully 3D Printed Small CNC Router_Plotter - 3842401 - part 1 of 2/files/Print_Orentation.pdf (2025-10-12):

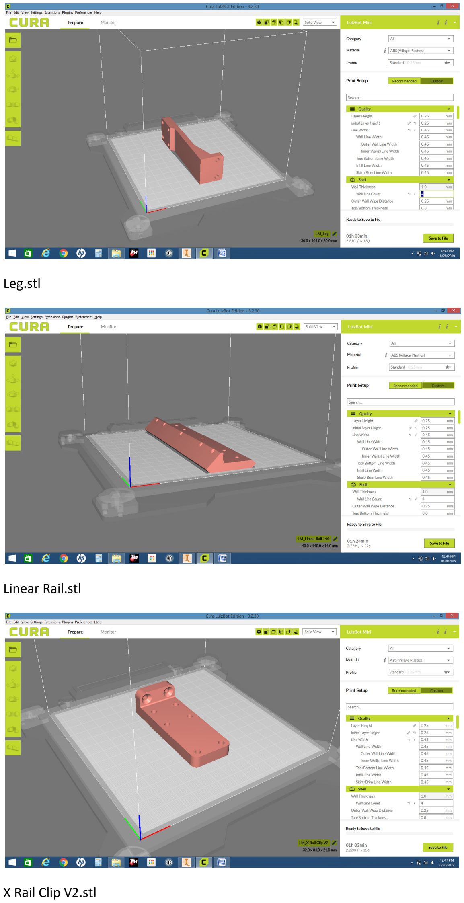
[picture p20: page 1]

Leg.stl

Linear Rail.stl

X Rail Clip V2.stl

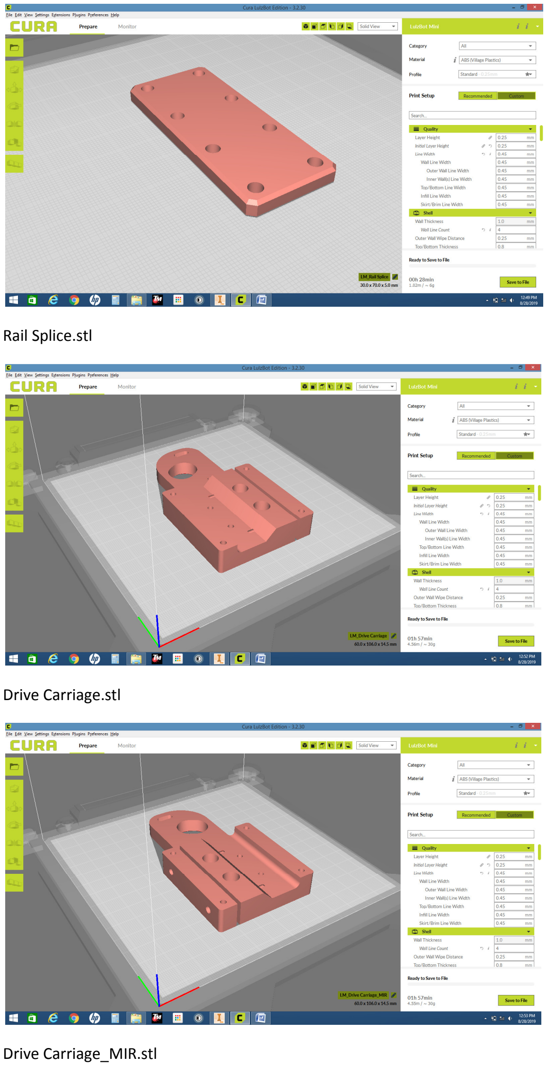
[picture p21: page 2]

Rail Splice.stl

Drive Carriage.stl

Drive Carriage_MIR.stl

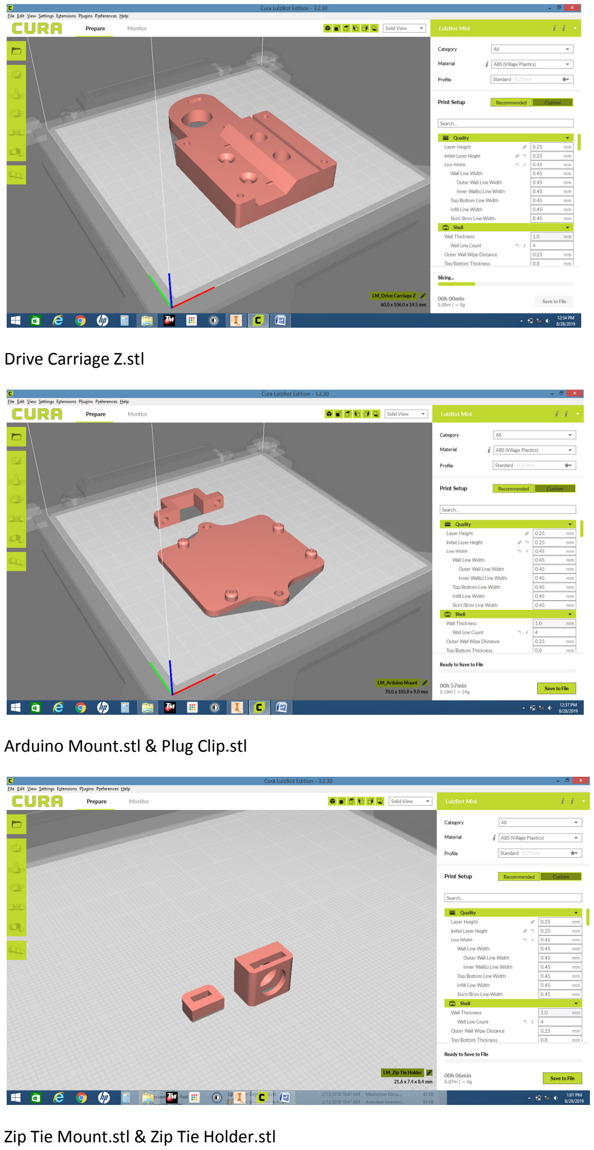
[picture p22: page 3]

Drive Carriage Z.stl

Arduino Mount.stl & Plug Clip.stl

Zip Tie Mount.stl & Zip Tie Holder.stl

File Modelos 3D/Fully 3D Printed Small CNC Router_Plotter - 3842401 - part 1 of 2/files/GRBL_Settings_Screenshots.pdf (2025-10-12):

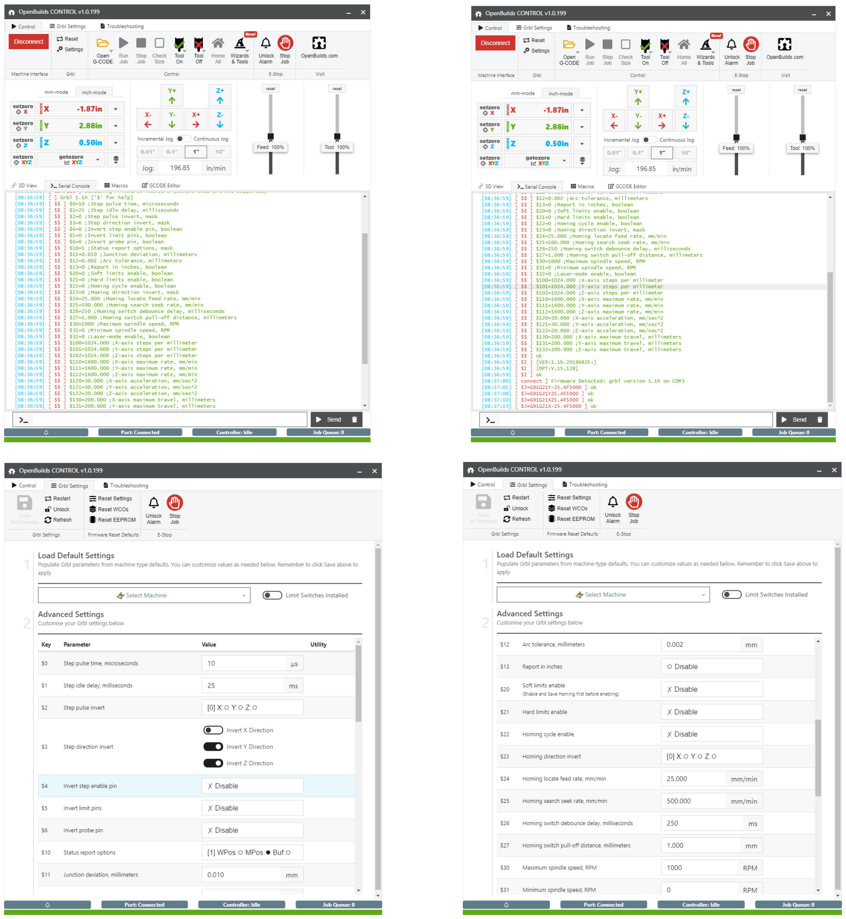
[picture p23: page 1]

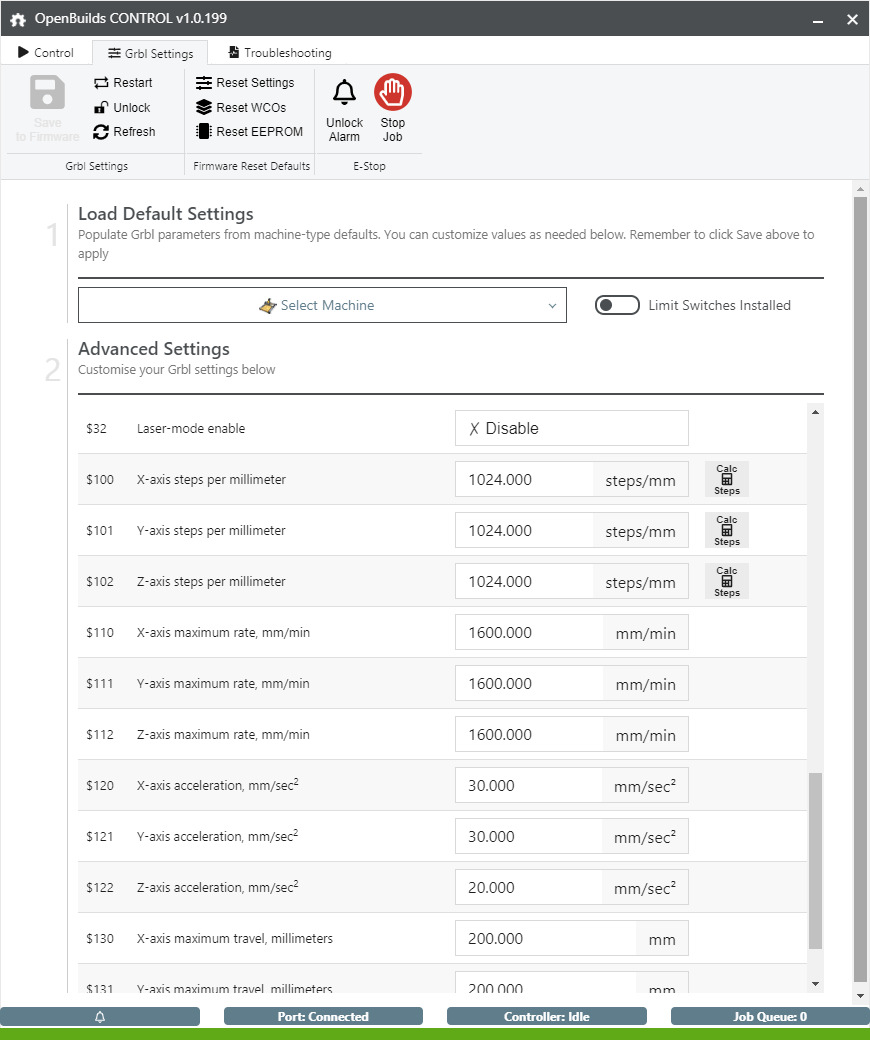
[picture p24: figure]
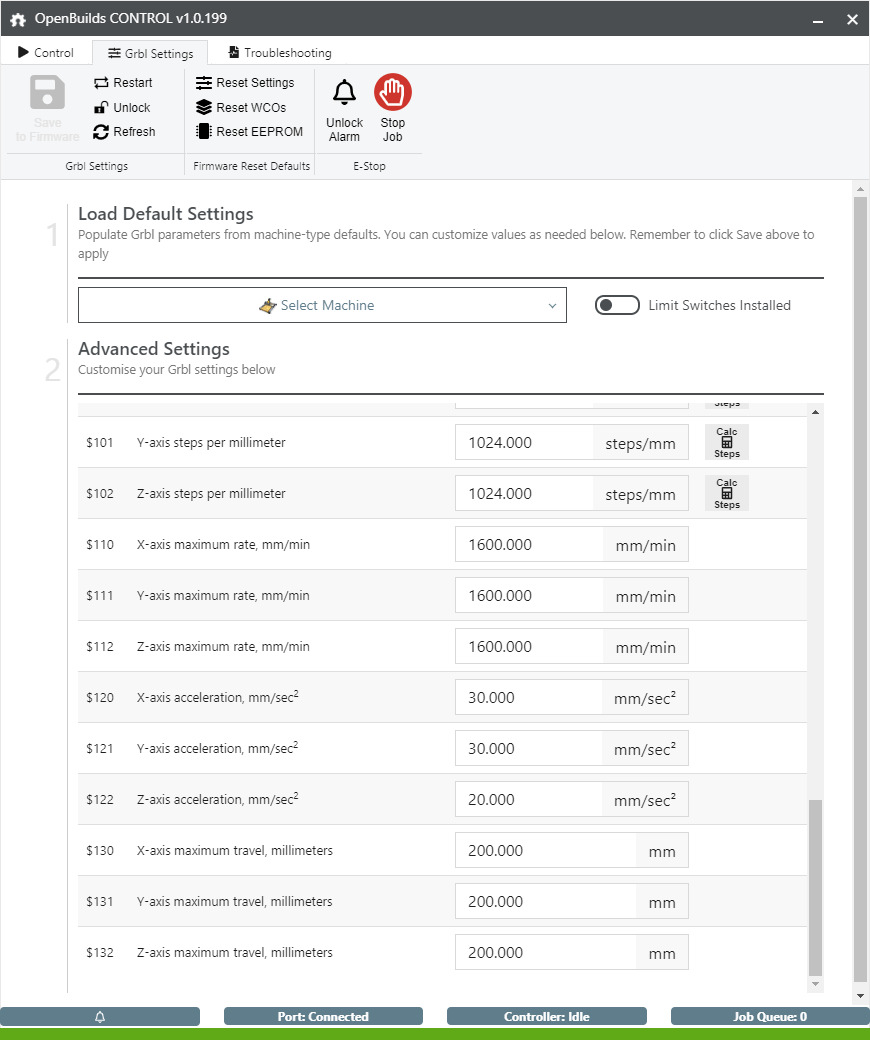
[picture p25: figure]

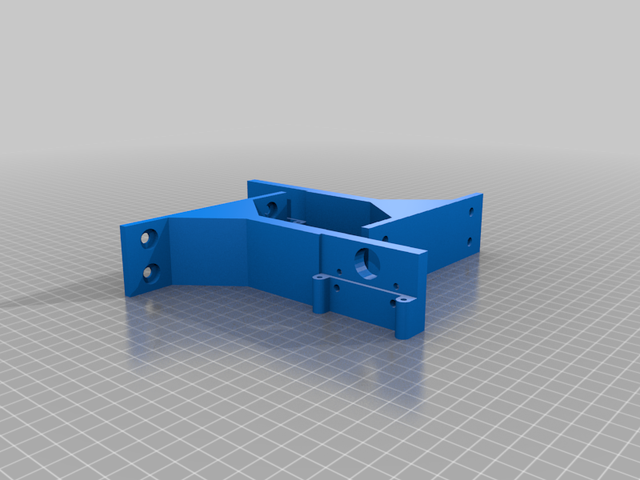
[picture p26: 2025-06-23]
Modelos 3D/English and Spanish Mini CNC Plotter With CNC SHIELD, Arduino and Step motor 28BYJ-28 - 2985627/images/efe20ff824f742c7bb8295f2e9ae51cf.png

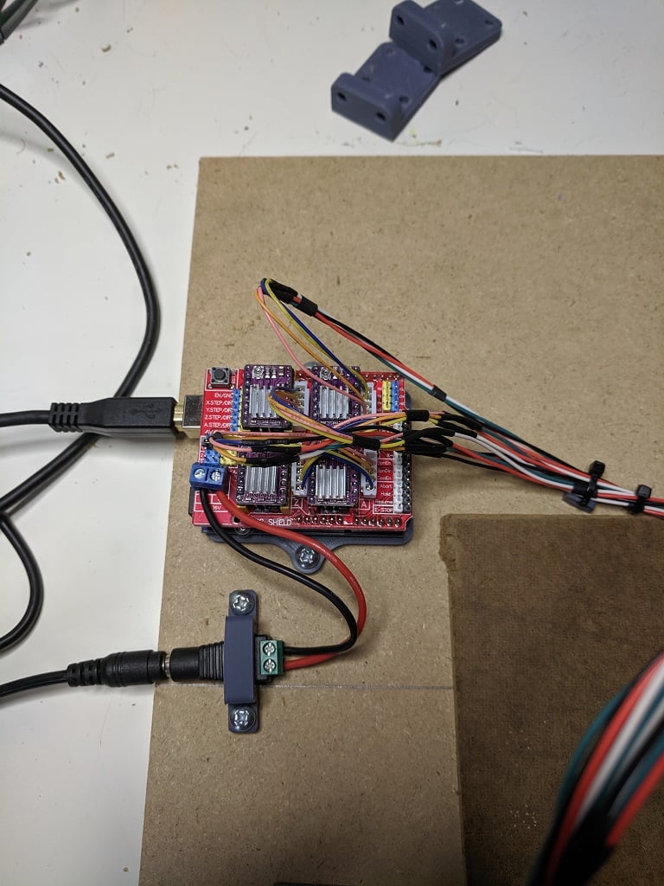
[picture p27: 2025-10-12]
Modelos 3D/Fully 3D Printed Small CNC Router_Plotter - 3842401 - part 1 of 2/images/Arduino_1-1.jpg

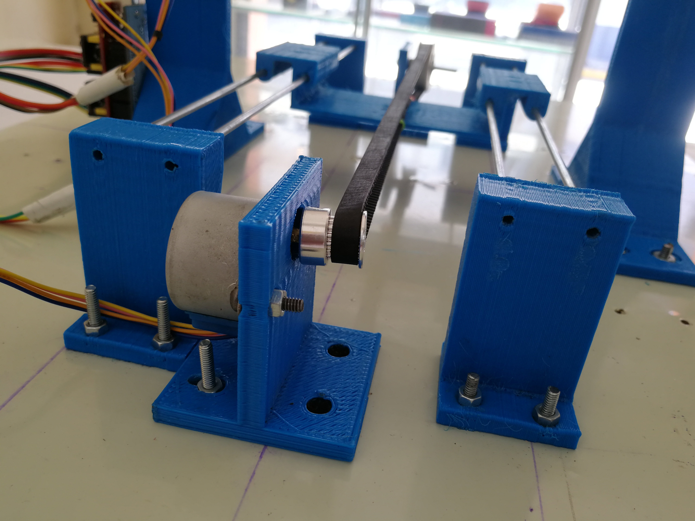
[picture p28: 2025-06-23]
Modelos 3D/English and Spanish Mini CNC Plotter With CNC SHIELD, Arduino and Step motor 28BYJ-28 - 2985627/images/IMG_20180701_112015.jpg

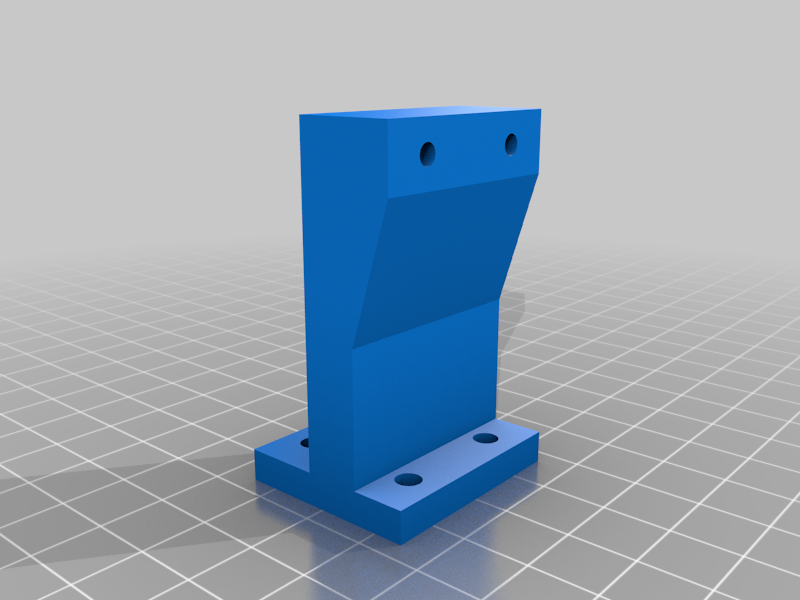
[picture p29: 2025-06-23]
Modelos 3D/English and Spanish Mini CNC Plotter With CNC SHIELD, Arduino and Step motor 28BYJ-28 - 2985627/images/61069694199e0b238a0622add471a211.png

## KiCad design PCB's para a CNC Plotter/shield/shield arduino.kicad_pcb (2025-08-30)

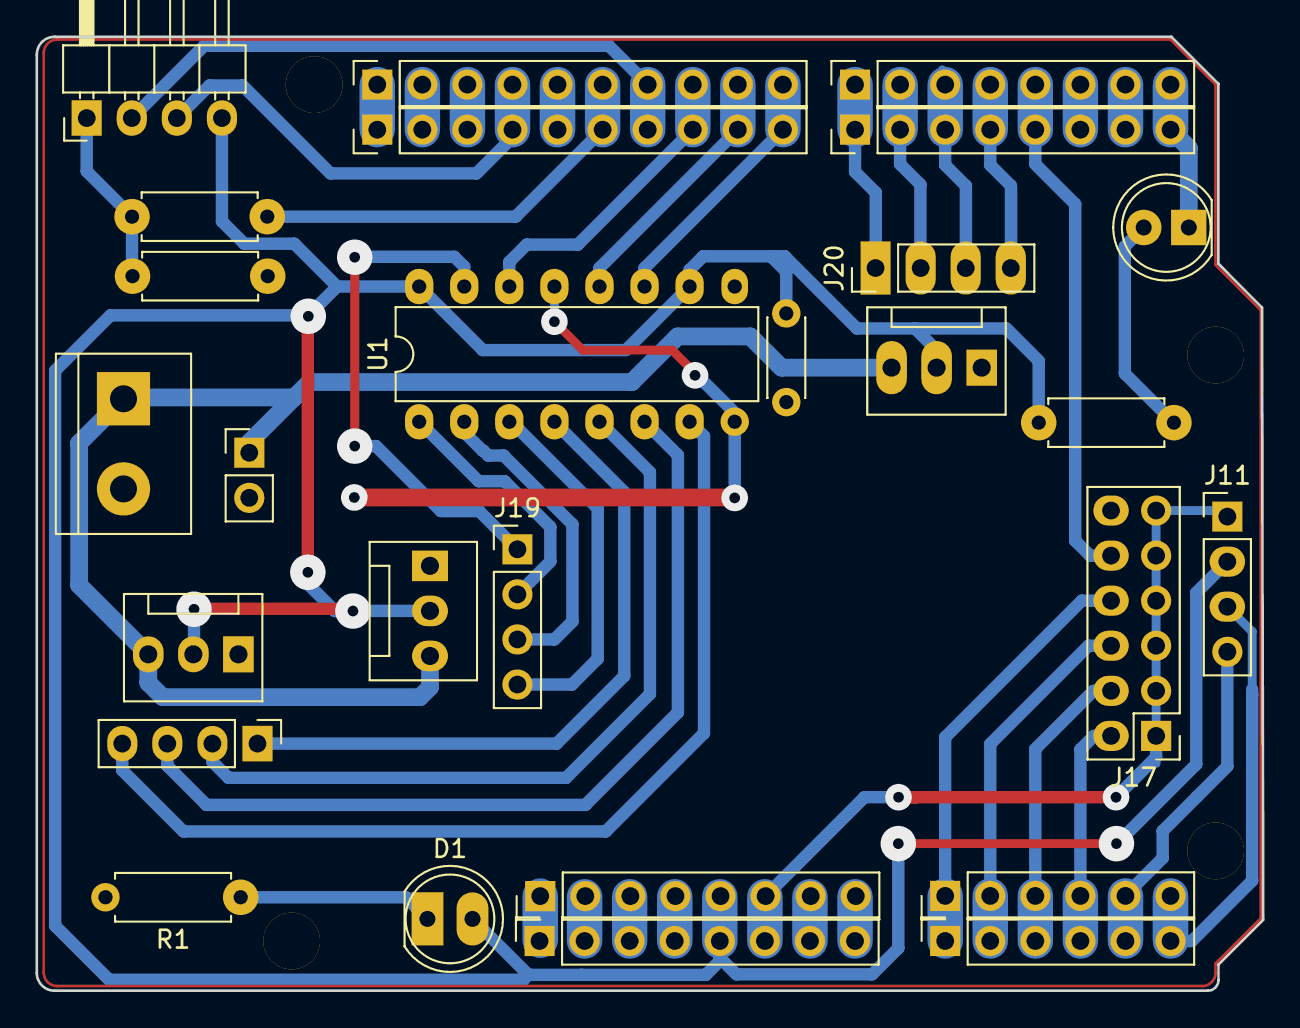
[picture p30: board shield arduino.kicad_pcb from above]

Board: 2 copper layers, 69.1 x 53.8 mm, 31 parts (0 on the bottom side), 38 nets.

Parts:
C4: 0.1uF; C_Disc_D4.3mm_W1.9mm_P5.00mm
D1, D2: LED; LED_D5.0mm
J1: Power; PinSocket_1x08_P2.54mm_Vertical
J2: Digital/PWM; PinSocket_1x10_P2.54mm_Vertical
J3: Analog; PinSocket_1x06_P2.54mm_Vertical
J4: Digital/PWM; PinSocket_1x08_P2.54mm_Vertical
J5: Vdrive; TerminalBlock_bornier-2_P5.08mm
J8: FAN; PinHeader_1x02_P2.54mm_Vertical
J10: Bluetooth; PinHeader_1x04_P2.54mm_Horizontal
J11: I2C; PinHeader_1x04_P2.54mm_Vertical
J12: MYF; PinHeader_1x04_P2.54mm_Vertical
J13: Power; PinHeader_1x08_P2.54mm_Vertical
J14: Analog; PinHeader_1x06_P2.54mm_Vertical
J15: Digital/PWM; PinHeader_1x10_P2.54mm_Vertical
J16: Digital/PWM; PinHeader_1x08_P2.54mm_Vertical
J17: Sensores; PinHeader_2x06_P2.54mm_Vertical
J18, J18#2, J18#3: Drivers VCC; FanPinHeader_1x03_P2.54mm_Vertical
J19: MXF; PinHeader_1x04_P2.54mm_Vertical
J20: MZF; PinHeader_1x04_P2.54mm_Vertical
MH1, MH2, MH3, MH4: MountingHole_3.2mm
R1: 4,7k; R_Axial_DIN0207_L6.3mm_D2.5mm_P7.62mm_Horizontal
R2, R4: 1k; R_Axial_DIN0207_L6.3mm_D2.5mm_P7.62mm_Horizontal
R3: 1.8k; R_Axial_DIN0207_L6.3mm_D2.5mm_P7.62mm_Horizontal
U1: 74HC595; DIP-16_W7.62mm

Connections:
+5V: C4.2, D1.2 (A), J1.5, J10.4, J11.2, J13.5, J17.12, J18.2, J18#2.2, J18#3.2, R4.1, U1.10 (~SRCLR), U1.16 (VCC)
/2: J4.6, J16.6
/4: J4.4, J16.4, J20.4
/7: J4.1, J16.1, J20.1
/8: J2.10, J15.10, U1.11 (SRCLK)
/12: J2.6, J15.6, R2.1
/13: J2.5, J15.5
/*3: J4.5, J16.5, J17.10
/*5: J4.3, J16.3, J20.3
/*6: J4.2, J16.2, J20.2
/*9: J2.9, J15.9, U1.12 (RCLK)
/*10: J2.8, J15.8, U1.14 (SER)
/*11: J2.7, J10.2, J15.7
/A0: J3.1, J14.1, J17.8
/A1: J3.2, J14.2, J17.6
/A2: J3.3, J14.3, J17.4
/A3: J3.4, J14.4, J17.2
/AREF: J2.3, J15.3
/IOREF: J1.2, J13.2
/RX/0: D2.1 (K), J4.8, J16.8
/SCL/A5: J2.1, J3.6, J11.3, J14.6, J15.1
/SDA/A4: J2.2, J3.5, J11.4, J14.5, J15.2
/TX/1: J4.7, J16.7
/Vin: J1.8, J13.8
/~RESET: J1.3, J13.3
Earth: C4.1, J1.6, J1.7, J2.4, J5.2, J8.2, J10.3, J11.1, J13.6, J13.7, J15.4, J17.1, J17.3, J17.5, J17.7, J17.9, J17.11, J18.1, J18#2.1, J18#3.1, R1.2, R3.1, U1.8 (GND), U1.13 (~OE)
unnamed: D1.1 (K), R1.1
unnamed: D2.2 (A), R4.2
unnamed: J10.1, R2.2, R3.2
unnamed: J12.1, U1.4 (QE)
unnamed: J12.2, U1.5 (QF)
unnamed: J12.3, U1.6 (QG)
unnamed: J12.4, U1.7 (QH)
unnamed: J19.1, U1.15 (QA)
unnamed: J19.2, U1.1 (QB)
unnamed: J19.3, U1.2 (QC)
unnamed: J19.4, U1.3 (QD)
Vdrive: J5.1, J8.1, J18.3, J18#2.3, J18#3.3

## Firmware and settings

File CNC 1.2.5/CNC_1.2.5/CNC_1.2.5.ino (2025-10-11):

/*
=====================================================================
  MINI CNC PLOTTER PARA CONFECÇÃO DE PLACAS DE CIRCUITO IMPRESSO
=====================================================================
  
  Autor: Geovane A. Silva
  Data de Criação: Janeiro de 2025
  Versão: 1.2.5
  
  Licença:
  Este código é distribuído sob a licença MIT, permitindo uso livre
  para qualquer finalidade, desde que seja mantida a atribuição ao autor.

*/

#include "stepMotor.h"
#include <SoftwareSerial.h>

#define TAMANHO_DA_LINHA 120                           // tamanho máximo de caracteres de uma linha
#define Xpos_mm (actuatorPos.x / passosPorMilimetroX)  // pos é a posição em mm
#define Ypos_mm (actuatorPos.y / passosPorMilimetroY)  // actuatorPos é a posição em passos

SoftwareSerial bluetooth(11, 12); // RX, TX

StepperSR StepperXY(PassosPorVolta, 8, 9, 10);
StepperSR StepperXYlevantado(PassosPorVolta, 8, 9, 10);
StepperSR StepperDebug(PassosPorVolta, 8, 9, 10);
Stepper StepperZ(PassosPorVolta, 7, 5, 6, 4);

const int PassosPorVolta = 200;
const int planner = 3;
const int bot = A0;

// Sensores de fim de curso
const int x0 = A1;
const int y1 = A2;

struct point {
    float x;
    float y;
    float z;
};

struct point actuatorPos;

// N° de passos para UP e DOWN da caneta:
const int penZUp = 80;
const int penZDown = -80;

const float passosPorMilimetroX = 23.57;
const float passosPorMilimetroY = 24.81;

// número de passos para X e Y considerado pequeno, sendo feito sem aceleração/desaceleração
const int movimentoCurto = round(passosPorMilimetroX * 2); // 2 milímetros

// Valores em milímetros do limite da área útil de impressão:
const float Xmin = 0.00, Xmax = 94.00;
const float Ymin = 0.00, Ymax = 83.00;
const float Zmin = 0.00, Zmax = 1.00;

int Zpos_mm = Zmax;
int caneta = 1;  // Iniciada em 1, pois a caneta inicialmente estará levantada.

int contagem = 0;

const int drawSpeed = 150;
const int moveSpeed = 250;

unsigned long timeOff;
unsigned long totalTime;

void setup() {

  pinMode(x0, INPUT_PULLUP);
  pinMode(y1, INPUT_PULLUP);
  pinMode(bot, INPUT_PULLUP);
  pinMode(planner, INPUT_PULLUP);

  StepperXY.setSpeed(drawSpeed);
  StepperXYlevantado.setSpeed(moveSpeed);
  StepperDebug.setSpeed(moveSpeed);
  StepperZ.setSpeed(150);

  //limitStep, mult
  StepperXY.         setAcel(30, 3);
  StepperXYlevantado.setAcel(120, 2);
  StepperDebug.setAcel(120, 2);

  StepperXY.Off();

  bluetooth.begin(9600); // Impossível comunicar com o módulo com baud rate acima de 9600, devido à alta taxa de falha no sinal
  Serial.begin(115200);
  Serial.println("Mini CNC Plotter a seu comando!");
  Serial.print("X vai de ");
  Serial.print(Xmin);
  Serial.print(" a ");
  Serial.print(Xmax);
  Serial.println(" mm.");
  Serial.print("Y vai de ");
  Serial.print(Ymin);
  Serial.print(" a ");
  Serial.print(Ymax);
  Serial.println(" mm.");

  // Cópia da mensagem de conexão
  bluetooth.println("Mini CNC Plotter a seu comando!");
  bluetooth.print("X vai de ");
  bluetooth.print(Xmin);
  bluetooth.print(" a ");
  bluetooth.print(Xmax);
  bluetooth.println(" mm.");
  bluetooth.print("Y vai de ");
  bluetooth.print(Ymin);
  bluetooth.print(" a ");
  bluetooth.print(Ymax);
  bluetooth.println(" mm.");
}


void loop() {

 receberLinha();

}

//============================ Funções ====================================

void receberLinha() {

  char linha[TAMANHO_DA_LINHA];  // Vetor que guardará a linha serial recebida.
  char c;                        // Auxiliar para verificar cada caractere.
  int posicao_linha = 0;         // Índice para controlar a posição do vetor 'linha'.
  bool LinhaComentada = false;   // Flag para identificar e ignorar comentários e ';' nas linhas recebidas.

  while (1) {

    if(millis() >= (timeOff + 50)) StepperXY.Off();

    while (Serial.available() > 0) {  // Enquanto houver dados na porta serial...
      c = Serial.read();              // Lê um caractere por vez.
      if ((c == '\n') || (c == '\r')) {
        if (posicao_linha > 0) {
          linha[posicao_linha] = '\0';  // Finaliza a string.
          processarLinha(linha, posicao_linha);
          posicao_linha = 0;
        }
        LinhaComentada = false;
        Serial.println("ok");  // Feedback para o código em Java.
      } else {
        if (LinhaComentada) {                  // Se estiver dentro de um comentário...
          if (c == ')') LinhaComentada = false;  // Fim do comentário.
        } else {
          if ((c == ' ')) {
          } // Ignora espaços
          else if (c == '(') {  // Início do comentário.
            LinhaComentada = true;
          }
          else if (posicao_linha >= TAMANHO_DA_LINHA - 1) {
            Serial.println("overload - lineBuffer chegou no limite de caracteres");
            LinhaComentada = false;
          }
          else if ((c >= 'a' && c <= 'z') || (c >= 'A' && c <= 'Z')) {  
            // Se for uma letra, insere um espaço antes (se não for o primeiro caractere)
            if (posicao_linha > 0) {
              linha[posicao_linha++] = ' ';
            }
            // Em seguida, insere a letra convertida para maiúscula, se necessário.
            if (c >= 'a' && c <= 'z') {
              linha[posicao_linha++] = c - 'a' + 'A';
            } else {
              linha[posicao_linha++] = c;
            }
          }
          else {
            linha[posicao_linha++] = c;
          }
        }
      }
    }
    while (bluetooth.available() > 0) {  // Enquanto houver dados na porta serial bluetooth...
      c = bluetooth.read();              // Lê um caractere por vez.
      if ((c == '\n') || (c == '\r')) {
        if (posicao_linha > 0) {
          linha[posicao_linha] = '\0';  // Finaliza a string.
          processarLinha(linha, posicao_linha);
          posicao_linha = 0;
        }
        LinhaComentada = false;
        bluetooth.println("ok");  // Feedback
      } else {
        if (LinhaComentada) {                  // Se estiver dentro de um comentário...
          if (c == ')') LinhaComentada = false;  // Fim do comentário.
        } else {
          if ((c == ' ')) {
          } // Ignora espaços
          else if (c == '(') {  // Início do comentário.
            LinhaComentada = true;
          }
          else if (posicao_linha >= TAMANHO_DA_LINHA - 1) {
            bluetooth.println("overload - lineBuffer chegou no limite de caracteres");
            LinhaComentada = false;
          }
          else if ((c >= 'a' && c <= 'z') || (c >= 'A' && c <= 'Z')) {  
            // Se for uma letra, insere um espaço antes (se não for o primeiro caractere)
            if (posicao_linha > 0) {
              linha[posicao_linha++] = ' ';
            }
            // Em seguida, insere a letra convertida para maiúscula, se necessário.
            if (c >= 'a' && c <= 'z') {
              linha[posicao_linha++] = c - 'a' + 'A';
            } else {
              linha[posicao_linha++] = c;
            }
          }
          else {
            linha[posicao_linha++] = c;
          }
        }
      }
    }
  }
}

void processarLinha(char* linha, int Numero_De_Caracteres) {

  struct point newPos;
  newPos.x = 0.0;
  newPos.y = 0.0;

  int verifica_X = 0;
  int verifica_Y = 0;
  int probe = 0;
  int mode = 0;

  float space = 0.0;
  float areaX = 0.0;
  float areaY = 0.0;
  
  // 1️⃣ Processa os comandos diretamente
  for (int i = 0; i < Numero_De_Caracteres; i++) {
    switch (linha[i]) {

      case 'M': {
        int valorM = atoi(&linha[i + 1]);  // Converte a substring para inteiro após 'M'

        switch (valorM) {
          case 114:  // M114 - Reportar posição atual
            Serial.print("Caneta na posicao : X = ");
            Serial.print(Xpos_mm);
            Serial.print("  -  Y = ");
            Serial.println(Ypos_mm);

            bluetooth.print("Caneta na posicao : X = ");
            bluetooth.print(Xpos_mm);
            bluetooth.print("  -  Y = ");
            bluetooth.println(Ypos_mm);
            break;
 
          case 18:  // M18 - Fim do desenho
            Serial.println("Desenho finalizado!!!");
            bluetooth.println("Desenho finalizado!!!");
            StepperXYlevantado.Off();
            StepperZ.Off();
            break;
          
          case 300:
            break;

          case 4: // M4 - Iniciar temporizador de contagem de tempo do desenho
            totalTime = millis();
            break;

          case 5: // M5 - Apresentar o tempo total do desenho
            totalTime = (millis() - totalTime) / 1000;
            unsigned long segundos = totalTime % 60;
            unsigned long minutos = (totalTime / 60) % 60;
            unsigned long horas = totalTime / 3600;
            
            Serial.print("Tempo desenhando: ");
            Serial.print(horas);
            Serial.print(":");
            Serial.print(minutos);
            Serial.print(":");
            Serial.println(segundos);

            bluetooth.print("Tempo desenhando: ");
            bluetooth.print(horas);
            bluetooth.print(":");
            bluetooth.print(minutos);
            bluetooth.print(":");
            bluetooth.println(segundos);
          break;

          default:
            Serial.print("Comando M desconhecido: M");
            Serial.println(valorM);

            bluetooth.print("Comando M desconhecido: M");
            bluetooth.println(valorM);
        }
        break;
      }

      case 'S': {

        int valorZ = atoi(&linha[i + 1]); 

        if(valorZ == 30) penDown();
        else if (valorZ == 50) penUp();
        break;
      }
      case 'Z': {

        int valorZ = atoi(&linha[i + 1]);

        if (valorZ <= 0)
          penDown();
        else
          penUp();
        break;
      }

      case 'C': {
        int valorN = atoi(&linha[i + 1]);        
          StepperZ.step(valorN);
          StepperZ.Off();
        break;
      }

      case 'U':  // Levanta a caneta
        StepperZ.step(penZUp);
        StepperZ.Off();
        Zpos_mm = Zmax;
        break;

      case 'D':  // Abaixa a caneta
        StepperZ.step(penZDown);
        StepperZ.Off();
        Zpos_mm = Zmin;
        break;
      
      case 'N': {
        int valorN = atoi(&linha[i + 1]); 
        
        switch (valorN) {
          case 1: // Espaço entre pontos
            while(i < Numero_De_Caracteres && linha[i] != 'S') i++;
            space = atof(&linha[i + 1]);
            break;

          case 2: // Tamanho da área de prova
            while(i < Numero_De_Caracteres && linha[i] != 'X') i++;
            areaX = atof(&linha[i + 1]);

            while(i < Numero_De_Caracteres && linha[i] != 'Y') i++;
            areaY = atof(&linha[i + 1]);
            probe = 1;
            break;
          
          case 3: // Apenas acelerar
            mode = 3;
            break;

          case 4: // Sem aceleração/desaceleração
            mode = 4;
            break;
          
          case 5: // Apenas desaceleração
            mode = 5;
            break;            
        }
      }
      break;

      case 'X':
      case 'Y': {
        if (linha[i] == 'X') {
          newPos.x = atof(&linha[i + 1]);  // Converte a substring para float após 'X'
          verifica_X = 1;
        } else {
          newPos.y = atof(&linha[i + 1]);  // Converte a substring para float após 'Y'
          verifica_Y = 1;
        }
        break;
      }
    }
  }

  // **2️⃣ Verifica se X e Y foram alterados antes de mover os motores**
  if (verifica_Y == 0) {
    newPos.y = Ypos_mm;
  }
  if (verifica_X == 0) {
    newPos.x = Xpos_mm;
  }

  if(probe == 1) probeMode(space, areaX, areaY);

  // Chamada da função que move os motores:
  drawLine(newPos.x, newPos.y, mode);

  // Reset de variáveis de controle:
  verifica_Y = 0;
  verifica_X = 0;

  timeOff = millis();
  //StepperXY.Off();
}



// **************************************************************************************************************************************************

// Função que move os motores para as coordenadas recebidas.
void drawLine(float targetX, float targetY, int mode) {

  // Limitação de coordenadas (em mm).
  targetX = (targetX >= Xmax) ? Xmax : (targetX <= Xmin) ? Xmin : targetX;
  targetY = (targetY >= Ymax) ? Ymax : (targetY <= Ymin) ? Ymin : targetY;

  // Converte as coordenadas de mm para passos.
  targetX = round(targetX * passosPorMilimetroX);
  targetY = round(targetY * passosPorMilimetroY);

  // Calcula a variação (em passos) entre a posição atual e a posição destino.
  int disX = abs(targetX - actuatorPos.x);
  int disY = abs(targetY - actuatorPos.y);

  // Determina a direção do movimento para cada eixo.
  int dirX = (actuatorPos.x < targetX) ? 1 : -1;
  int dirY = (actuatorPos.y < targetY) ? 1 : -1;
  
  // Utilização de referências &stepperX e &stepperY para facilitar o código
  StepperSR &motor = caneta ? StepperXYlevantado : StepperXY;

  long over = 0;
  int corrigido = 0;
  int n = (disX > disY) ? disX : disY;  // Número de iterações = maior entre disX e disY

  bool canGoX;
  bool canGoY;

  if(disX <= movimentoCurto && disY <= movimentoCurto)
    motor.resetAcelParameters(n, 4);
  else 
    motor.resetAcelParameters(n, mode);

  for (int i = 0; i < n; i++) {

      // Verificação de correção de posição
      if (verify() && !corrigido) {
        corrigido = 1;
        contagem = 0;
      }
      else corrigido = 0;
    contagem++;

    motor.aceleration(i);

    // Eixo principal: X
    if (disX >= disY) {
      canGoX = true;
      actuatorPos.x += dirX;
      over += disY;
      if (over >= disX) {
        over -= disX;
        canGoY = true;
        actuatorPos.y += dirY;
      }
    } // Eixo principal: Y
    else {
      canGoY = true;
      actuatorPos.y += dirY;
      over += disX;
      if (over >= disY) {
        over -= disY;
        canGoX = true;
        actuatorPos.x += dirX;
      }
    }
    motor.oneStep(canGoX, canGoY, dirX, dirY);
    canGoX = false;
    canGoY = false;
  }
} // Fim de drawLine

// **************************************************************************************************************************************************

int verify() {
      
    bool canGoX;
    bool canGoY;
    int pen = caneta;

    if (((!digitalRead(x0) || !digitalRead(y1) || !digitalRead(bot))) || contagem == 10000) {
      // Pause
      if (!digitalRead(bot)) {
        StepperDebug.Off();
        delay(500);
        while (digitalRead(bot)) {}
      }

      if (!pen) {
      penUp();
      }

      for(int i = 0; i < 2; i ++) {
      // Move os eixos até os sensores
      while (digitalRead(x0) || digitalRead(y1)) {
        
        if (digitalRead(x0)) canGoX = true;
          else canGoX = false;
        if (digitalRead(y1)) canGoY = true;
          else canGoY = false;

        StepperDebug.oneStep(canGoX, canGoY, -1, 1);
      }
      delay(150);
      // Move os eixos até desativar os sensores (posição home)
      while (!digitalRead(x0) || !digitalRead(y1)) {
        
        if (!digitalRead(x0)) canGoX = true; 
          else canGoX = false;
        if (!digitalRead(y1)) canGoY = true;
        else canGoY = false;

        StepperDebug.oneStep(canGoX, canGoY, 1, -1);
      }
      delay(150);
      }
      int contadorX = abs(actuatorPos.x - (Xmin * passosPorMilimetroX));
      int contadorY = abs((Ymax * passosPorMilimetroY) - actuatorPos.y);

      long over = 0;
      int n = (contadorX > contadorY) ? contadorX : contadorY;  // Número de iterações = maior entre contadorX e contadorY
      
      StepperDebug.resetAcelParameters(n, 5);

      for (int i = 0; i < n; i++) {
        StepperDebug.aceleration(i);

      if (contadorX >= contadorY) {
          // Eixo principal: X
          canGoX = true;
          over += contadorY;
          if (over >= contadorX) {
              over -= contadorX;
              canGoY = true;
          }
      } 
      else {
        // Eixo principal: Y
        canGoY = true;
        over += contadorX;
        if (over >= contadorY) {
            over -= contadorY;
            canGoX = true;
        }
      }
      StepperDebug.oneStep(canGoX, canGoY, 1, -1);
      canGoX = false;
      canGoY = false;
    }
      if (!pen) {
        penDown();
      }
      return 1;
    }
    else return 0;
}


// **************************************************************************************************************************************************

void penUp() {

  if (!caneta) {
    StepperXY.Off();
    StepperZ.step(penZUp);
    StepperZ.Off();

    Zpos_mm = Zmax;
    caneta = 1;
  }
}

// **************************************************************************************************************************************************

void penDown() {

  if (caneta) {
    StepperXY.Off();
    StepperZ.step(penZDown);
    StepperZ.Off();

    Zpos_mm = Zmin;
    caneta = 0;
  }
}

// **************************************************************************************************************************************************

void probeMode(float space, float areaX, float areaY) {

  areaX = (areaX >= Xmax) ? Xmax : (areaX <= Xmin) ? Xmin : areaX;
  areaY = (areaY >= Ymax) ? Ymax : (areaY <= Ymin) ? Ymin : areaY;
  
  drawLine(0.0, 0.0, 0);
  StepperXY.Off();
  
  while(digitalRead(planner) == 1) {
    StepperZ.step(-1);
    delay(5);
  }
  StepperZ.step(penZUp);

  for (float y = 0.0; y <= areaY; y += space) {
    for (float x = 0.0; x <= areaX; x += space) {
      int stepC = 0;  // Inicializa a cada ponto de sondagem

      drawLine(x, y, 0);
      StepperXY.Off();
 
      while(digitalRead(planner) == 1) {
          StepperZ.step(-1);
          stepC++;
          delay(5);
      }

      // Retorna o eixo Z à posição original
      StepperZ.step(stepC);
      StepperZ.Off();
      
      stepC -= penZUp;
      stepC = -stepC;
      
      Serial.print("X");
      Serial.print(x);
      Serial.print(" Y");
      Serial.print(y);
      if(stepC > 0) Serial.print(" C+");
      else Serial.print(" C");
      Serial.println(stepC);
    }
  }
  StepperZ.step(-20);
  StepperZ.Off();
}

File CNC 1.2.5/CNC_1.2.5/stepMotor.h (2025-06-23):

/*
=====================================================================
  Biblioteca para Controle de Motor de Passo Unipolar com Half-Step
=====================================================================
  
  Autor: Geovane A. Silva
  Data de Criação: Fevereiro de 2025
  Versão: 1.2
  
  Licença:
  Este código é distribuído sob a licença MIT, permitindo uso livre
  para qualquer finalidade, desde que seja mantida a atribuição ao autor.

*/

#ifndef STEPPER_H
#define STEPPER_H

class Stepper {

private:

  //============================== Variáveis =======================================
  
  int StepperPins[4];
  int passosPorVolta;
  int currentStep;           // grava em qual passo da matriz o motor parou
  
  long stepDelay;            // Delay entre passos
  unsigned long lastTime;    // Marca de tempo do último passo
  
  int acel;
  int limitStep;
  int limitStepMin;
  long speed;
  int midStep;
  long maxSpeed;
  long minSpeed;
  //===============================================================================
  /*
  // Sequência para meio-passo
  const int halfStepSequence[8][4] = {
    { 0, 1, 1, 0 },
    { 0, 1, 0, 0 },
    { 0, 1, 0, 1 },
    { 0, 0, 0, 1 },
    { 1, 0, 0, 1 },
    { 1, 0, 0, 0 },
    { 1, 0, 1, 0 },
    { 0, 0, 1, 0 }
  }; */

  // Sequência para modo inteiro
  /*const int fullStepSequence[4][4] = {
    { 0, 1, 1, 0 },
    { 0, 1, 0, 1 },
    { 1, 0, 0, 1 },
    { 1, 0, 1, 0 }
  };
  */
  // Sequência para modo de meio-passo ordenado
  const int halfStepSequence[8][4] = {
    { 1, 0, 0, 0 },
    { 1, 1, 0, 0 },
    { 0, 1, 0, 0 },
    { 0, 1, 1, 0 },
    { 0, 0, 1, 0 },
    { 0, 0, 1, 1 },
    { 0, 0, 0, 1 },
    { 1, 0, 0, 1 }
  };
  const int fullStepSequence[4][4] = {
    { 1, 1, 0, 0 },
    { 0, 1, 1, 0 },
    { 0, 0, 1, 1 },
    { 1, 0, 0, 1 }
  };

public:

Stepper(int passosPorVolta, int pin1, int pin2, int pin3, int pin4) {

    this->passosPorVolta = passosPorVolta;
    this->StepperPins[0] = pin1;
    this->StepperPins[1] = pin2;
    this->StepperPins[2] = pin3;
    this->StepperPins[3] = pin4;

    for (int i = 0; i < 4; i++) {
      pinMode(this->StepperPins[i], OUTPUT);
      digitalWrite(this->StepperPins[i], LOW);
    }
}

void setSpeed(long rpm) {

    stepDelay = (60000000L / passosPorVolta / rpm) / 2;
}

void setSpeedFull(long rpm) {

    stepDelay = (60000000L / passosPorVolta / rpm);
}

void step(int steps) {

    int stepsLeft = abs(steps);
    int direcao = (steps > 0) ? 1 : -1;

    while (stepsLeft > 0) {

      unsigned long actualTime = micros();
      if (actualTime - lastTime >= stepDelay) {

        lastTime = actualTime;
        currentStep += direcao;

        if (currentStep >= 8) currentStep = 0;
        if (currentStep < 0) currentStep = 7;

        for (int i = 0; i < 4; i++) {
          digitalWrite(StepperPins[i], halfStepSequence[currentStep][i]);
        }

        stepsLeft--;
      }
    }
}

void stepFull(int steps) {

    int stepsLeft = abs(steps);
    int direcao = (steps > 0) ? 1 : -1;

    while (stepsLeft > 0) {

      unsigned long actualTime = micros();
      if (actualTime - lastTime >= stepDelay) {

        lastTime = actualTime;
        currentStep += direcao;

        if (currentStep >= 4) currentStep = 0;
        if (currentStep < 0) currentStep = 3;

        for (int i = 0; i < 4; i++) {
          digitalWrite(StepperPins[i], fullStepSequence[currentStep][i]);
        }

        stepsLeft--;
      }
    }
}

void Off() {  // Função usada para manter os motores desligados durante delays pelo código main.

    for(int i = 0; i < 4; i++) {
      digitalWrite(this->StepperPins[i], LOW);
    }
}

long Delay() {
  return stepDelay;
}

void setAcel(int limitStep, int mult) {
  this-> acel = (stepDelay * mult) / limitStep;
  this-> limitStep = limitStep;
  this-> minSpeed = stepDelay * mult;
  this-> maxSpeed = stepDelay;
}

void resetAcelParameters(int n) {
  this-> speed = minSpeed;
  this-> limitStepMin = n - limitStep;
  this-> midStep = n / 2;
}

void aceleration(int i) {  
  if(i < midStep && speed > maxSpeed && i <= limitStep) {
    speed -= acel;
    delayMicroseconds(speed);
  }
  else if(i > midStep && speed < minSpeed && i >= limitStepMin) {
    speed += acel;
    delayMicroseconds(speed);
  }
  else delayMicroseconds(speed);
}

};  // End class


class StepperSR {

private:

/*
const int halfStepSequence[8][4] = {
  { 1, 0, 0, 0 },
  { 1, 1, 0, 0 },
  { 0, 1, 0, 0 },
  { 0, 1, 1, 0 },
  { 0, 0, 1, 0 },
  { 0, 0, 1, 1 },
  { 0, 0, 0, 1 },
  { 1, 0, 0, 1 }
};
*/

const byte halfStepSequence[16] = {
// Motor 1 (Qa - Qd)
  0b10000000,
  0b11000000,
  0b01000000,
  0b01100000,
  0b00100000,
  0b00110000,
  0b00010000,
  0b10010000,
// Motor 2 (Qe - Qh)
  0b00001000,
  0b00001100,
  0b00000100,
  0b00000110,
  0b00000010,
  0b00000011,
  0b00000001,
  0b00001001
};

const byte halfStepSequenceBresenham[9] = {
  0b1000,
  0b1100,
  0b0100,
  0b0110,
  0b0010,
  0b0011,
  0b0001,
  0b1001,
  0b0000
};

//============================== Variáveis =======================================
int currentStepX;
int currentStepY;
int oneCurrentStepX;
int oneCurrentStepY;
unsigned long stepDelay;
int passosPorVolta;

int DATA;
int CLOCK;
int LATCH;

int acel;
int limitStep;
int maxStep;
long maxSpeed;
long minSpeed;

unsigned long lastTime;

int mode;
int mult;

int teste1 = 0;
int teste2 = 0;
//===============================================================================

public:

StepperSR(int passosPorVolta, int CLOCK, int LATCH, int DATA) {
  this->passosPorVolta = passosPorVolta;
  this->DATA = DATA;
  this->CLOCK = CLOCK;
  this->LATCH = LATCH;

  pinMode(DATA, OUTPUT);
  pinMode(CLOCK, OUTPUT);
  pinMode(LATCH, OUTPUT);
  digitalWrite(DATA, LOW);
  digitalWrite(CLOCK, LOW); 
  digitalWrite(LATCH, LOW); 
}

void setSpeed(long rpm) {
    stepDelay = (60000000L / passosPorVolta / rpm) / 2;
}

void step(int steps, char motor) {

  int stepsLeft = abs(steps);
  int direcao = (steps > 0) ? 1 : -1;
  unsigned long startTime;

  while (stepsLeft > 0) {
    startTime = micros();

    if (startTime - lastTime >= stepDelay) {

      if (motor == 'X' || motor == 'x') {
        currentStepX += direcao;
        if (currentStepX >= 8) currentStepX = 0;
        if (currentStepX < 0) currentStepX = 7;
        shiftOut(DATA, CLOCK, LSBFIRST, halfStepSequence[currentStepX]);
      }
      if (motor == 'Y' || motor == 'y') {
        currentStepY += direcao;
        if (currentStepY >= 16) currentStepY = 8;
        if (currentStepY < 8) currentStepY = 15;
        shiftOut(DATA, CLOCK, LSBFIRST, halfStepSequence[currentStepY]);
      }
      digitalWrite(LATCH, HIGH);
      digitalWrite(LATCH, LOW);
      stepsLeft--;
      lastTime = micros();
    }
  }
}
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

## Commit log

2025-06-23 Envio dos arquivos do projeto
    [E.stl, Soporte_para_lapiz.stl, Spindle_Holder.stl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]
2025-06-24 Modificação no README e na pinagem do arduino
2025-06-24 Organização de arquivos e versionamento de códigos.
2025-07-17 Removido arquivos Gerbers antigos
    [shield arduino.kicad_pcb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]
2025-08-30 v1.2.5 — Lançamento: correções e melhorias
    [shield arduino.kicad_pcb, shield arduino.kicad_sch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]
2025-10-11 Atualização de firmware e adição do APP CNC Plotter Sender
    [shield arduino.kicad_pcb, shield arduino.kicad_sch]
2025-10-12 Update do ReadMe.md e modificações de código
    [Arduino_Mount.stl, Drive_Carriage.stl, Drive_Carriage_MIR.stl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]
